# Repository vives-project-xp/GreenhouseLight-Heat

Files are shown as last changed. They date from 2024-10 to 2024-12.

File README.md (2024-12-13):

# GreenhouseLight-Heat

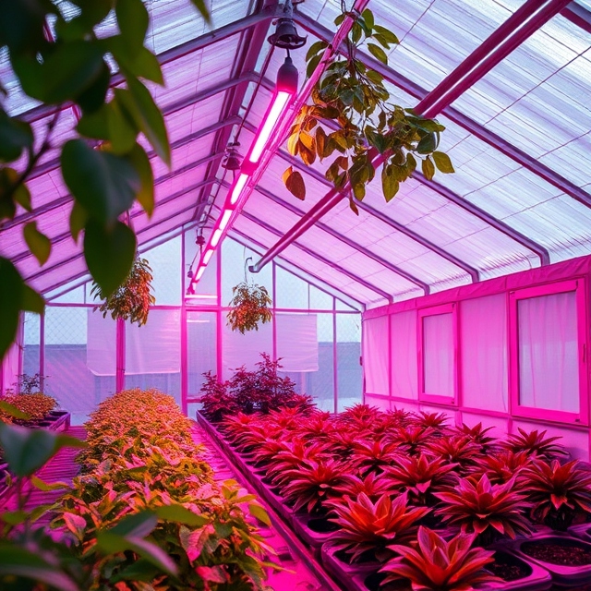
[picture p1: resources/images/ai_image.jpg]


## Introduction

This project automates the control of light and heat within a greenhouse to optimize plant growth year-round. Through a network of sensors and actuators, the system continuously monitors and adjusts environmental conditions to create the ideal environment for plants. We don't do everyting on or own we have a group that measure the temprature and light intensity. And one that send us the data.

[GreenhouseSensoring](./Documentatie/README.md).

[GreenhouseNetwork-Monitoring](https://github.com/vives-project-xp/GreenhouseNetwork-Monitoring).

## Our team

- Thibaut Schroyens (SCRUM Master)
- Sam De Wispelaere
- Joren Vandewalle

## features

- **Light Control:** Automated purple lightning based on the current lightintensity.
- **Temperature Regulation:** Monitors greenhouse temperature, controlling electric heaters to add warmth and a shade cloth to try and cooldown the serre.
- All LEDs, heaters, and actuators run on standard power (230V), making installation straightforward and accessible without specialized wiring.

## Hardware

- **ledstrip:** SK6812 RGBW LED Strip 5m
- **esp32:** ESP32-C3-DevKitC-02
- **voedingen:** Mean Well Rs-50-5 (5V-10A) + Mean Well UHP-200R-36 (36V-5.6A)
- **stappenmotor:** SY42STH47-1206A 
- **level shifter:** Sparkfun Logic converter, bi-directional
- **heater:** VONROC heater marsili compact -2000W
- **Smart plug :** Wiz Smart plug
- **stepper motor driver:** Joy-it SBC-MD-TB6600
- **Shade cloth**
- **Lamp construction**
- **Shade cloth roll-up construction**

### Hardware architecture diagram

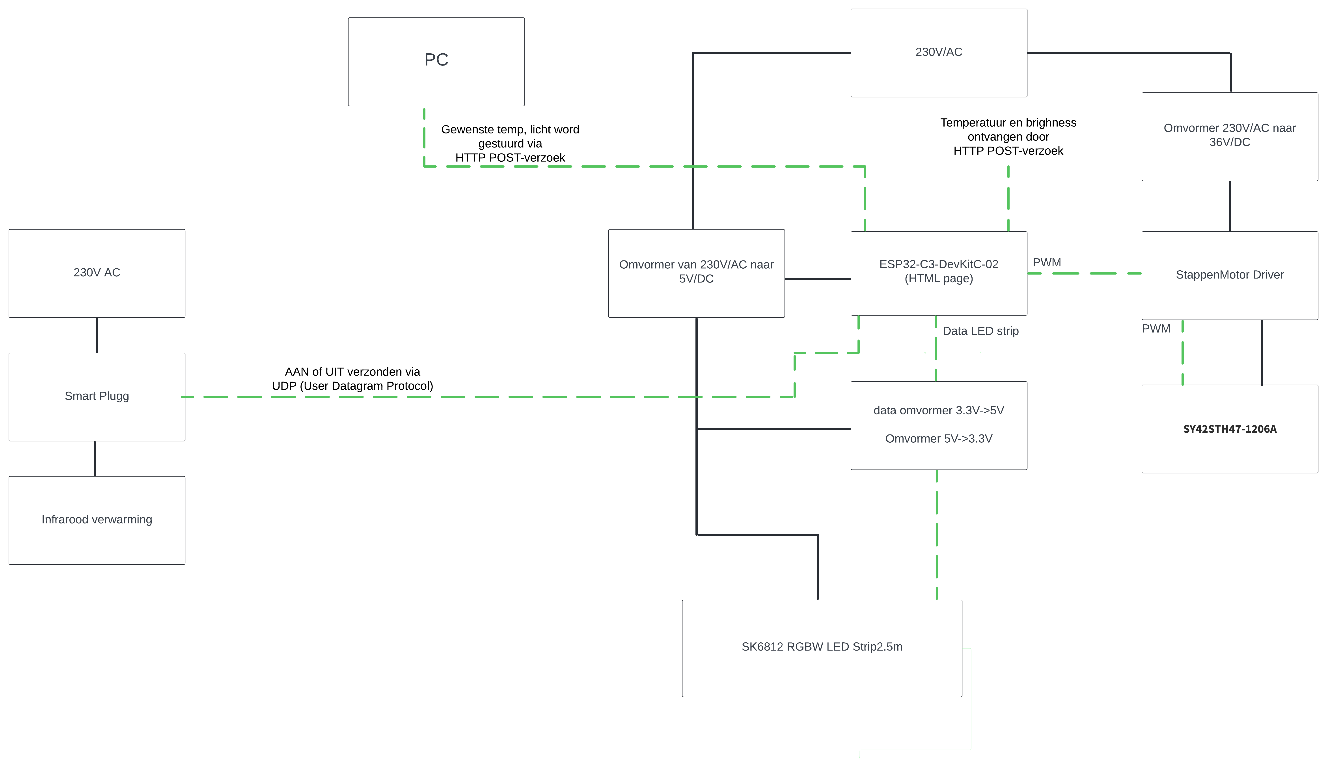
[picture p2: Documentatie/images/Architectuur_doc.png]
Architectuur_Doc


## Software

- We flash all the code on the ESP using  [Arduino IDE](https://www.arduino.cc/en/software). 

We use there settings for our ESP32 in IDE

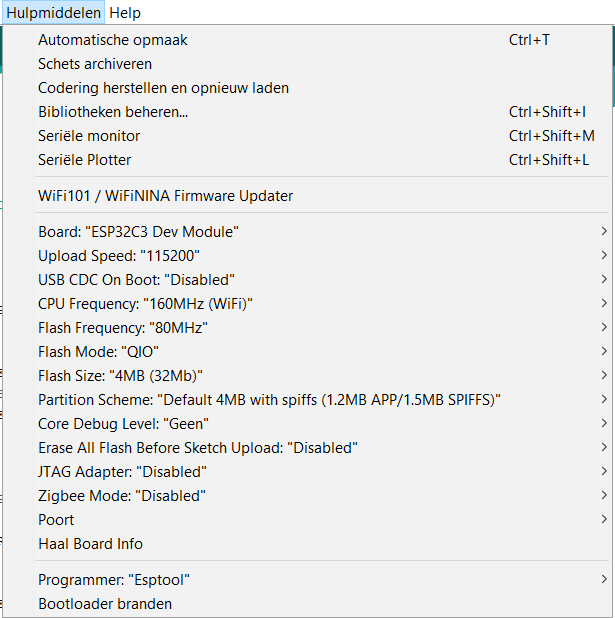
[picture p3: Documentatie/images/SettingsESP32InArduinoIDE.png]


### Used librarys
- **WebServer.h:** Handles HTTP server requests
- **ArduinoJson.h:** Parses incoming JSON data.
- **WiFi.h:** Connects the ESP32 to a Wi-Fi network
- **FastLED.h:** Controls the LED strip.
- **WiFiUdp.h:** Used to communicate with the WiZ smart plug via UDP.

## Bom list

These are all the components we purchased in this project. **Prices may vary depending in the website and date!!**

| Component | Quantity | Price / unit |
| :--- | :---: | ---: |
| [**SK6812 RGBW LED Strip**](https://www.btf-lighting.com/collections/sk6812-rgbw/products/1-sk6812-rgbw-4-in-1-pixels-individual-addressable-led-strip-dc5v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) | 1 | €36,36 |
| [**ESP32-C3-DevKitC-02**](https://www.digikey.be/nl/products/detail/espressif-systems/ESP32-C3-DEVKITC-02/14553009) | 1 | €7,12 |
| [**stappenmotor**](https://www.pololu.com/product/1200l) | 2 | €25,63 |
| [**verwarmingselement**](https://www.brico.be/nl/tuin-terras-buitenleven/terrasverwarming/terrasverwarmers-accessoires/terrasverwarmers/vonroc-heater-marsili-compact-2000w-zwart/10138731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) | 1 | €41,28 |
| [**level shifter**](https://www.kiwi-electronics.com/nl/sparkfun-logic-level-converter-bi-directional-3154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) | 1 | €3,51 |
| [**Omvormer 230-5**](https://www.conrad.be/nl/p/mean-well-rs-50-5-schakelnetvoedingsmodule-5-v-dc-10-a-50-w-1297303.html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) | 1 | €14,04 |
| [**Smart plug**](https://www.hubo.be/nl/p/wiz-smart-plug-stekker/943560/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) | 1 | €13,21 |
| [**Stappenmotordriver**](https://www.conrad.be/nl/p/joy-it-sbc-md-tb6600-stappenmotordriver-2999126.html?refresh=true) | 1 | €19,83 |
| [**voeding driver**](https://www.conrad.be/nl/p/mean-well-uhp-200r-36-schakelnetvoedingsmodule-36-v-dc-5-6-a-201-6-w-2237833.html) | 1 | €54,54 |

## Step by step plan

For a step by step installition guide click [here](./Documentatie/README.md).

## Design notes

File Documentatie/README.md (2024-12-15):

# Installation

## Reviece the data

Before we start we need to be abled to connect the ESP32 to the Wifi and recieve the data from [GreenhouseNetwork-Monitoring](https://github.com/vives-project-xp/GreenhouseNetwork-Monitoring) 

- For this we had to place  [this code snipped](../Code/Sending_date.py) in there code. For more info go to there Github.

- Now to connect the ESP32 to the Wifi and recieve the date we u need to upload [this code snipped](../Code/ResieveData_And_No_WLED/ResieveData_And_No_WLED.ino)  to the esp.

### Postman
- If u dont want to use the other projects or u want to test things without them u can test the ESP32 using [Postman](https://www.postman.com/)

Using these settings: 
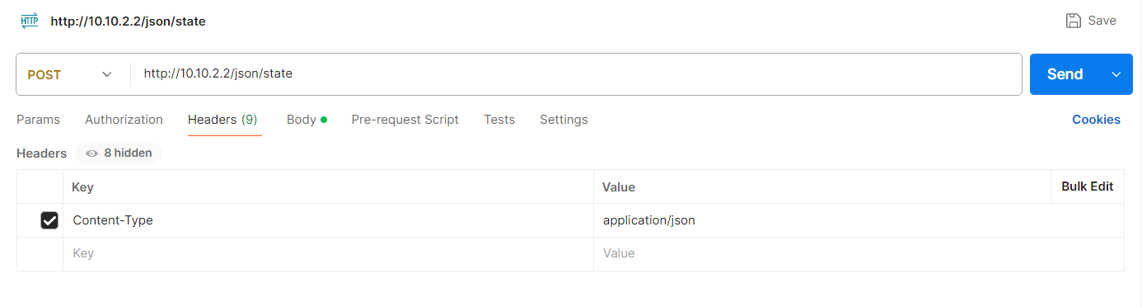
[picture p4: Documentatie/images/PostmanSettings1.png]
Postman1

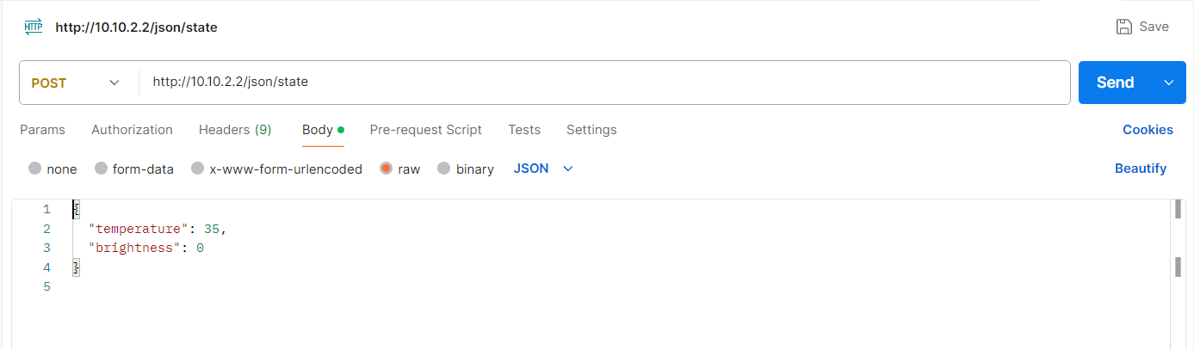
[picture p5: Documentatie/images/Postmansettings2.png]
Postman2


Now u shoud be abled to send the data to ur ESP. 

## Step by step guide

1. **Install the LED strip/Lamp:** this can all be found [here](./Lamp_Install_Guide/README.md)
2. **Install shade Shade cloths:** how to install them can be found here [here](./Shade_cloths_Install_Guide/README.md).
3. **Install heater:** if u want to know how we installed the heater that can be found here [here](./Heater_Install_Guide/README.md).

**Its a good thing to test everyting together in a demo setup before u install things on the actual serre!!!** 

The final code can be found [here](../Code/TotalCode/TotalCode.ino).

### HTML page
Last minute we also put a small HTML page on our ESP , so we can change the wanted temprature in the serre without needing to touch the ESP. If u want to add the HTML page aswell [its this code](../Code/TotalCode/TotalCodeWithHTML/TotalCodeWithHTML.ino) 

### Electrical diagram

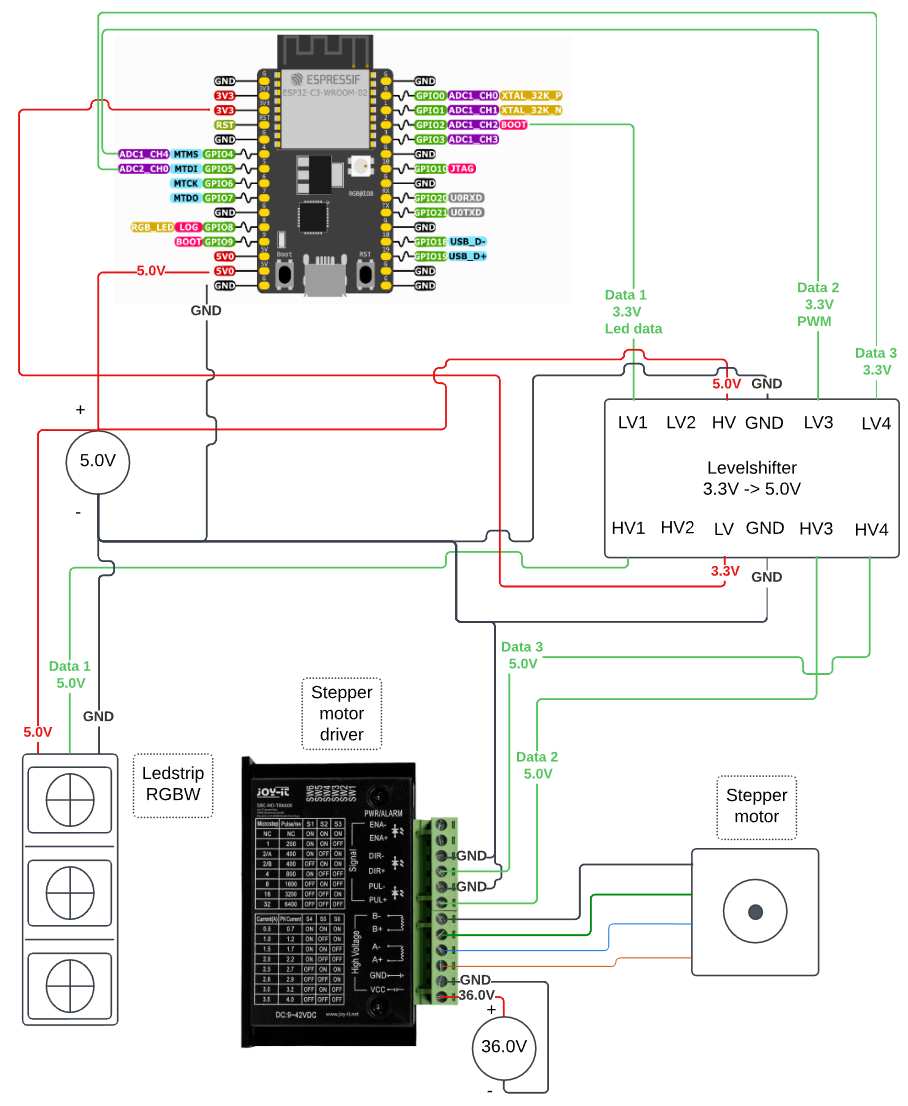
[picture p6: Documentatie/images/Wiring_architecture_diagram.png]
Architectuur_Doc

connections_circuit
connections_circuit

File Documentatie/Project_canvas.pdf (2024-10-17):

Project name GreenhouseLight-Heat | Project owner Vives

Purpose

Whatis the intent ofthis project? Why are we doing this project?

Scope

What does this project contain? What does this project not contain?

| Success Criteria What do we need to achieve in orderfor the project to be successful? How can the Success Criteria be measured?

Milestones

When will we startthe project and when is the final deadline ? What are the key milestones and when willthey occur?
How can the milestones be measured?

Outcome

Whatis the end
result?
- A book
- A website
- An event

Actions

Which activities need to be executed in order to reach a certain milestone?

Team Thibaut Schroyens (Project leader) Who are the team members? What are theirroles in the project? Sam De Wispeleare Joren Vandewalle | Stakeholders Who has an interest in the success of the project? In what way are they involved in the project? Vives | Users Who will benefitfrom the outcome ofthe project? Future students interested in learning about automating processes.
Resources LED lighting, sun-blocking fabric, What resources do we need in the project? - Physical (office, building, server) 12 weeks of work, budget of 175 - Financial (money) euros, positive team. - Human (time, knowledge) | Constraints What are the known limitations ofthe project? - Physical (office, building, server) - Financial (money) -Human (time, knowledge, politics) Money, time, large surfaces. | Risks Which risks may occur during the project? How do we treat these risks? Humidity/wet environment combined with electrical components.
Copyright © Project Canvas | www.projectcanvas.dk

Optimize the growth of plants by adjusting light and heat.

Light and heat regulation.

A fully automated system that optimizes the growth of plants.

Sprint 1: Brainstorming, concept development. Drafting the architecture document, creating a small prototype. Finalize the architecture document, place orders. (3 weeks)
Sprint 2: Working prototype, refined architecture document, final approval. (3 weeks)
Sprint 3: Completed product or proof of concept, thorough documentation, user manual. (3 weeks)
Sprint 4: Product tested, presentation. (2 weeks)
- Research techniques for regulating heat and light.
- Look into how everything can be mounted or installed.
- Explore how to automate the entire system.
- Identify and order the necessary products.
- Document everything as thoroughly as possible.
- Build a prototype to identify where adjustments are needed.

A fully
automated
system that
regulates
temperature
and light in the
greenhouse.

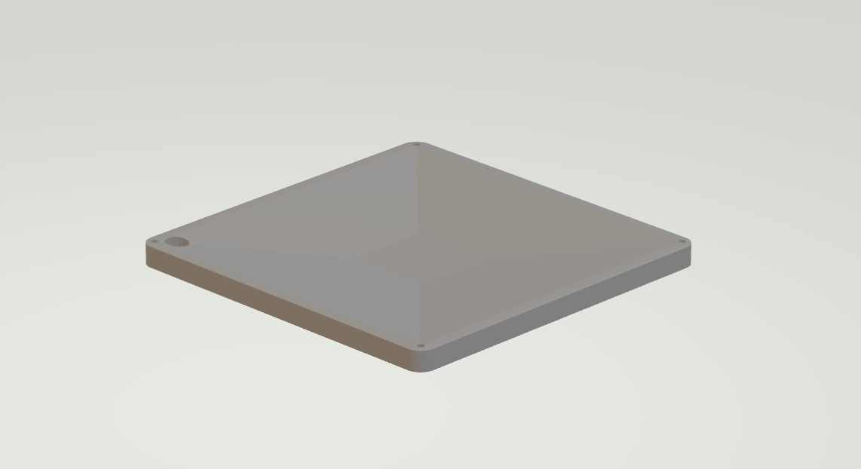
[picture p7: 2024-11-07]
resources/images/LampPlaat.png

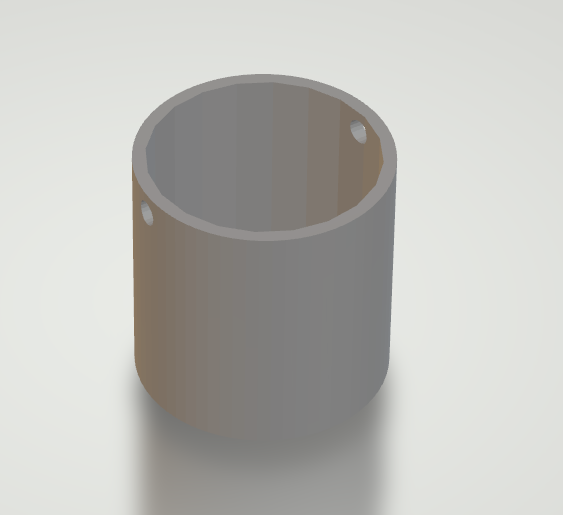
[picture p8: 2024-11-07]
resources/images/WeightForDirt.png

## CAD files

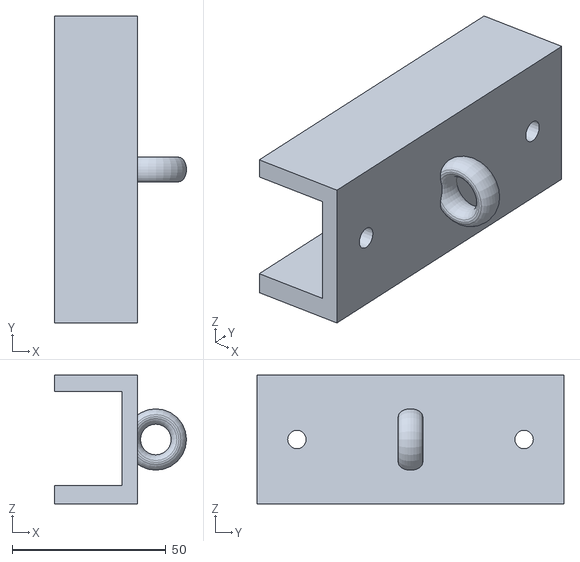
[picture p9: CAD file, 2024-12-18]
resources/3D-Tekeningen/lamp_mount_AND_weight_holder.stl
43.0 x 100.0 x 42.0

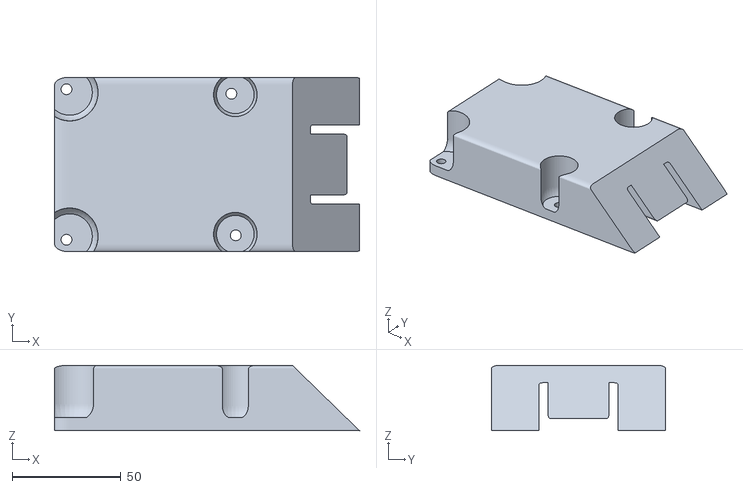
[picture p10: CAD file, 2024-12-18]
resources/3D-Tekeningen/motor_mount_backplate.stl
140.0 x 80.0 x 30.0

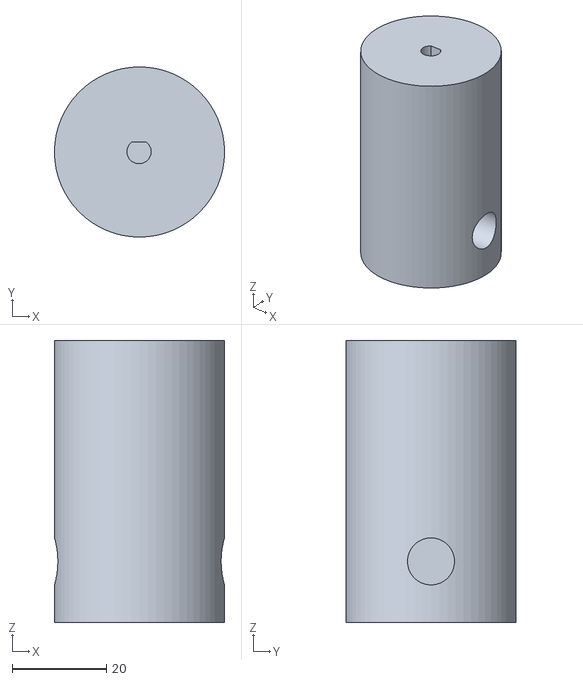
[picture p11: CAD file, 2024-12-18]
resources/3D-Tekeningen/buizen_motor_connect.stl
36.2 x 36.2 x 60.0

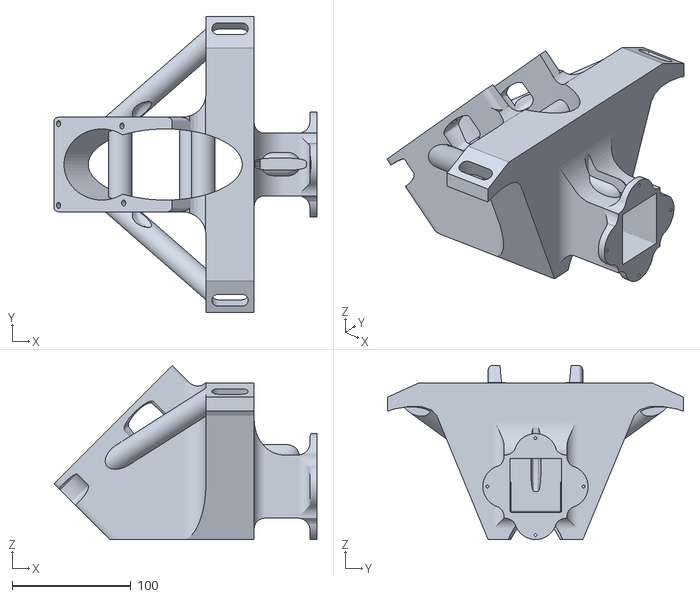
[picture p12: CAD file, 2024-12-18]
resources/3D-Tekeningen/motor_mount.stl
221.9 x 250.0 x 146.9

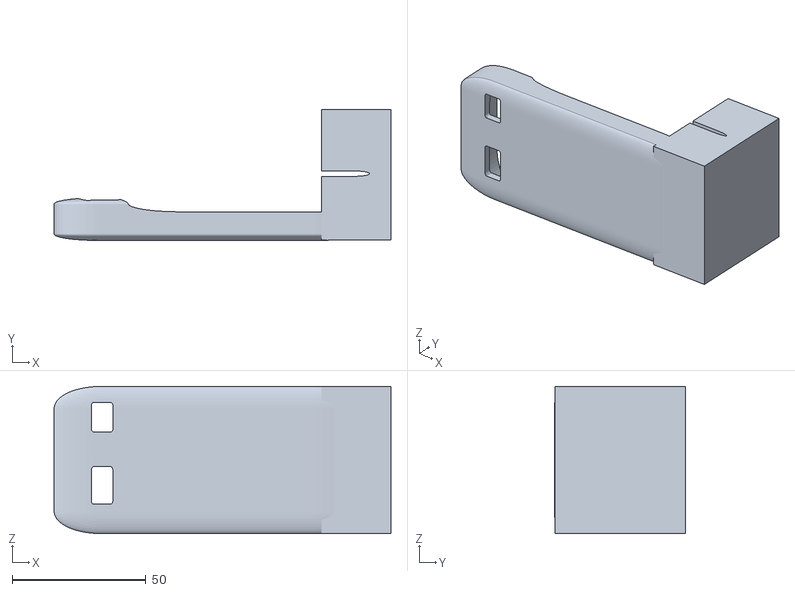
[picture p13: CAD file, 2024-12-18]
resources/3D-Tekeningen/verwarming_mount.stl
126.0 x 49.0 x 55.0

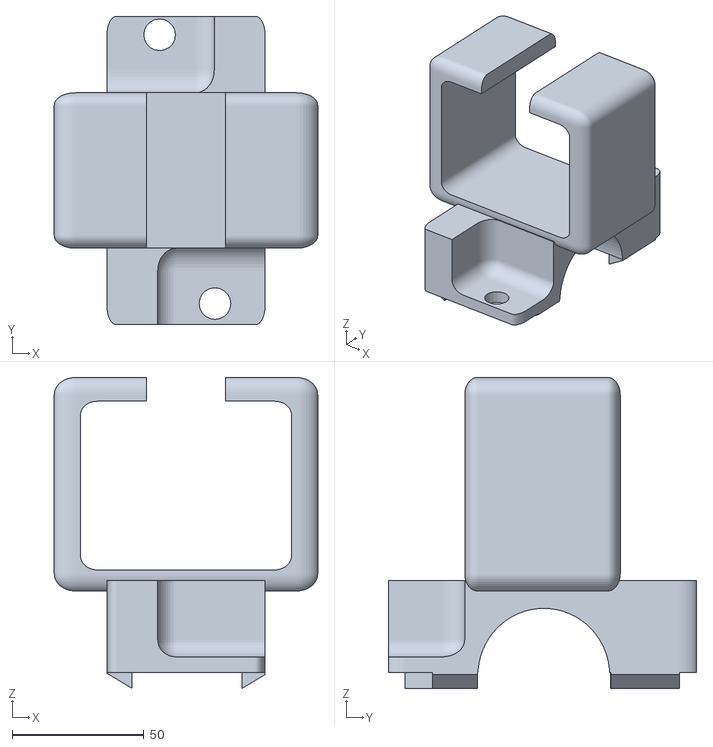
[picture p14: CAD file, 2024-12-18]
resources/3D-Tekeningen/buis_bottom_camera_mount.stl
100.0 x 117.0 x 118.0

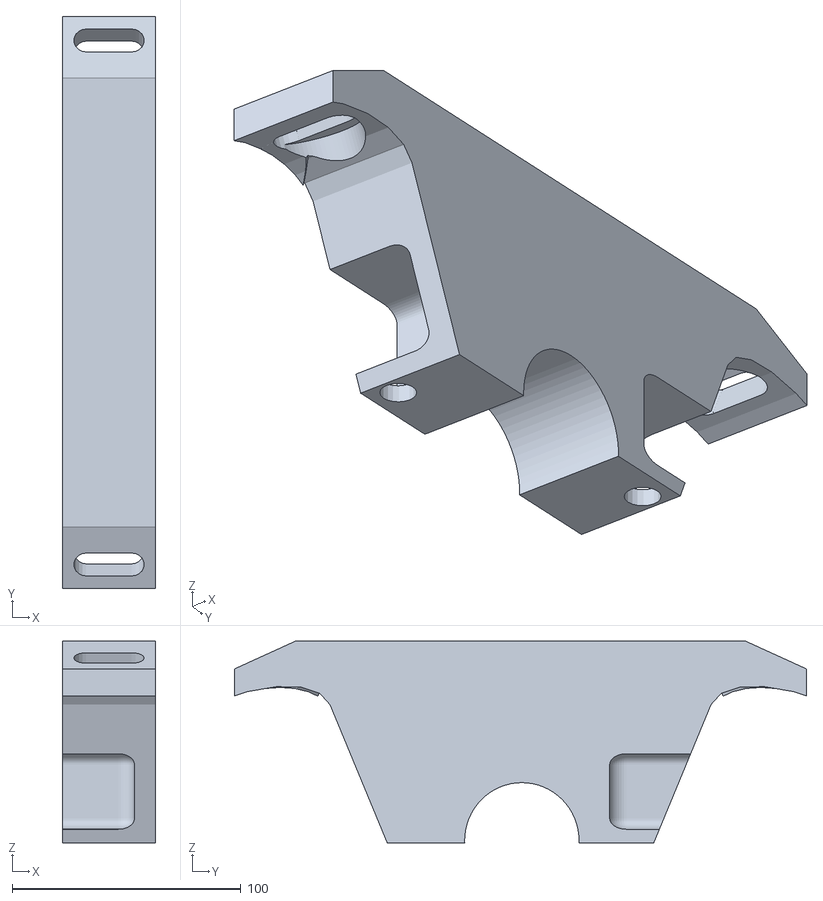
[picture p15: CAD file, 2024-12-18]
resources/3D-Tekeningen/buis_top_camera_mount.stl
40.7 x 250.0 x 88.3

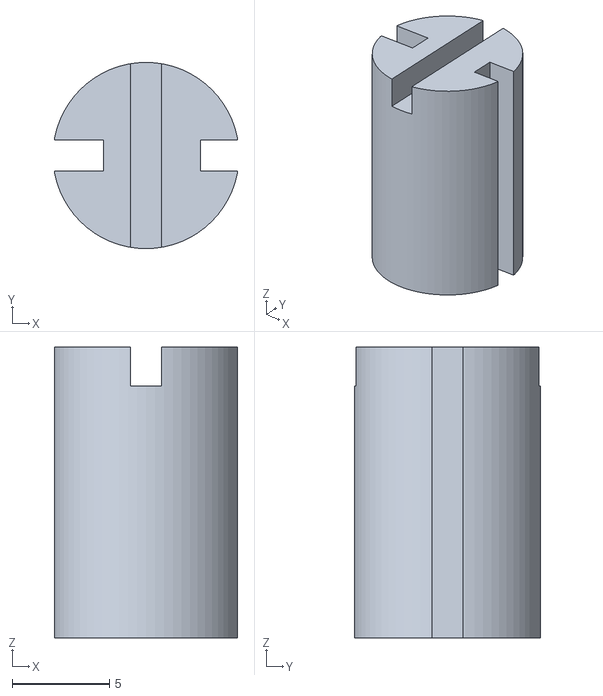
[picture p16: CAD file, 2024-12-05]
resources/3D-Tekeningen/buizen_connector_pins.stl
9.46 x 9.60 x 15.0

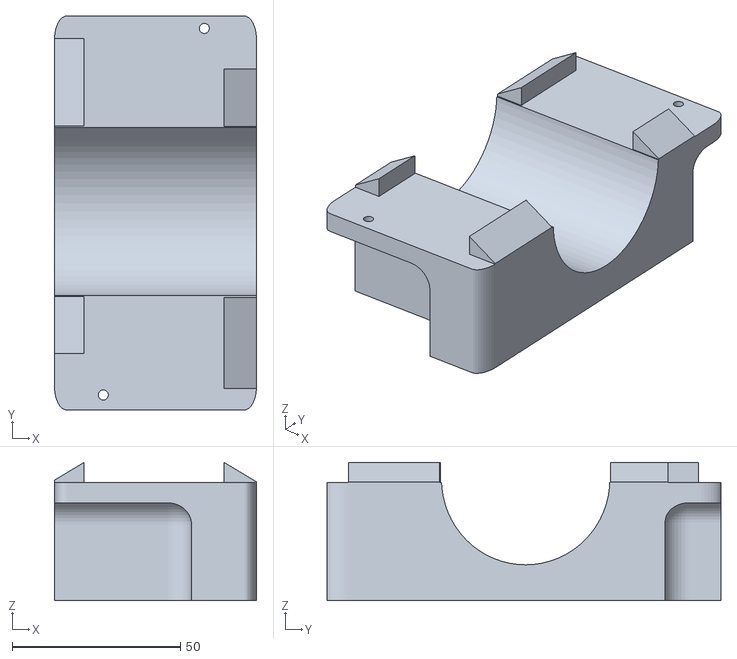
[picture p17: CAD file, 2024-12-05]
resources/3D-Tekeningen/buis_support_bottom.stl
60.0 x 117.0 x 41.0

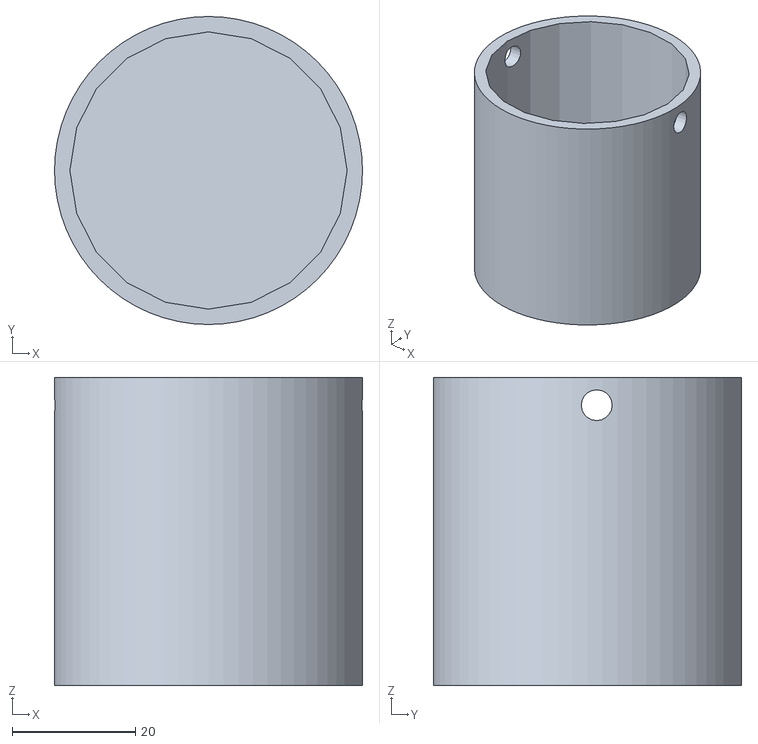
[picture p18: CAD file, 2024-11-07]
resources/3D-Tekeningen/WeightForDirt.stl
50.0 x 50.0 x 50.0

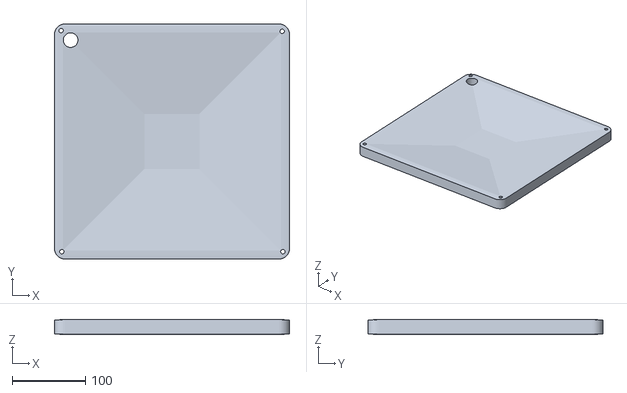
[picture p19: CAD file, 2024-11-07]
resources/3D-Tekeningen/PlaatLamp.stl
320.0 x 320.0 x 20.0

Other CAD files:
resources/3D-Tekeningen/lamp_mount.stl
resources/3D-Tekeningen/buis_support_top.stl
resources/3D-Tekeningen/buizen_connector.stl

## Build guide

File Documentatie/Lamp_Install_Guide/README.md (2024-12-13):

# Install LED strip/Lamp

## Requirements

1. **ledstrip: SK6812 RGBW LED Strip 5m**
2. **SparkFun Logic Level Converter - Bi-Directional**
3. **Soldering material** (Soldering iron, Tin)
4. **ESP32 Microcontroller**
5. Connection cables

## Step 1: Cut and Prepare the LED Strip

Start by cutting the LED strip into 2.5-meter sections. Afterward, cut each 2.5-meter piece into smaller segments, each containing 16 LEDs, resulting in 9 pieces in total.

Next, solder the segments together. Make sure to connect the following:

- **Data (Date)** to **Data Input (Din)**
- **Do (Data Output)** to **Din (Data Input)**
- **GND** to **GND** (Ground)

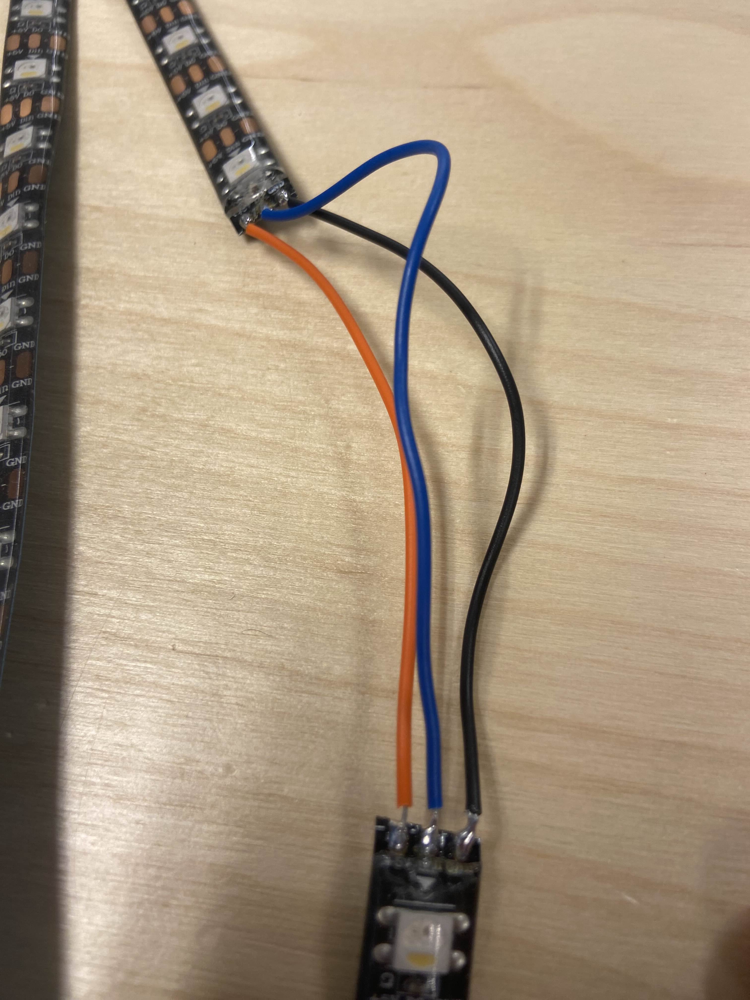
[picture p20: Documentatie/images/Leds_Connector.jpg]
leds_connector


This will ensure that the LED strip is properly configured for your project.

This should be the final result:

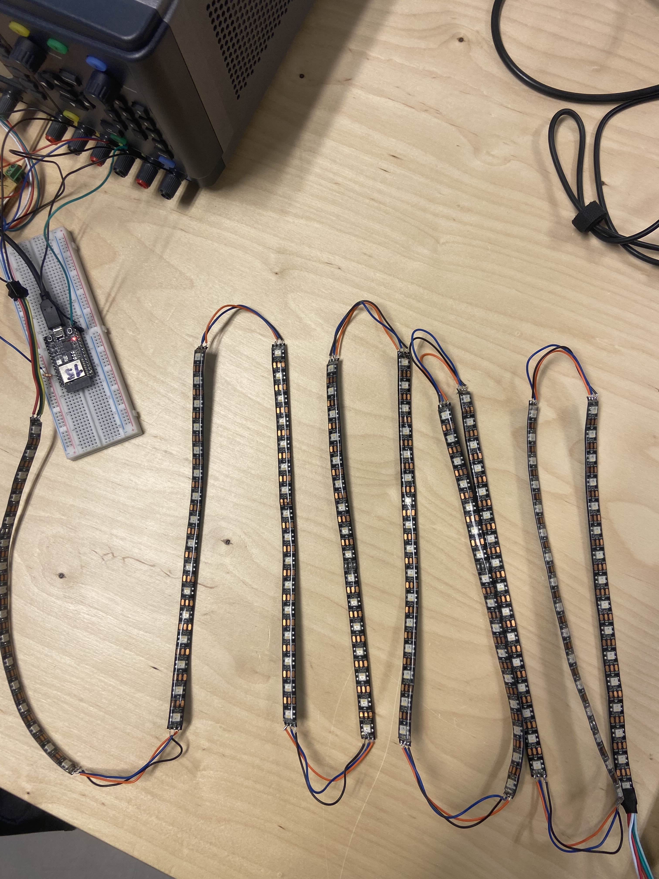
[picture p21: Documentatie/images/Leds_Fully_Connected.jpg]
leds_fully_connected


## Step 2: Connect the LED strip to the ESP32

### Electrical schema

eletrical_schema

electrical_circuit

---

### Guide on Connections

To properly connect the components, we need to use a **3.3V to 5V level shifter** because the ESP32 sends **3.3V data signals**, while the LED strips require **5V data signals**. We made or own custom board for this.

#### Power Supply

- The **5V power source** is used for two purposes:
  1. Supplying power to the **level shifter**.
  2. Feeding power to both the **ESP32** and the **LED strips**.

#### GPIO Connections

- The **LED strip** is connected to **GPIO2** on the ESP32 (via the level shifter).

By ensuring this configuration, the ESP32 can reliably control the LED strips without voltage mismatches.

connections_circuit
connections_circuit

## Step 3: Code

Initially, we considered using **WLED** because it is easy to set up and manage. However, we also needed to implement our custom script on the ESP32 to control the **heater** and **shading**. Since integrating WLED with our custom logic proved challenging, we decided to manage the LEDs through our own script instead. This approach allows us to consolidate all sensor data and control logic.

Then to test the basic LED setup u can [upload this code](../../Code/LEDS_Aanstuuren/LEDS_Appart_Aanstuuren.ino) to ur esp32 this should give u purple light on the LEDS.

## Step 4: Connect the ESP to Net current

## Step 5: Installation on serre

### Led strip on lamp

Now the ledstrip can be put onto the [3d printed lamp](../../resources/3D-Tekeningen/PlaatLamp.stl). You put the ledstrip on the plate of the lamp so that the connector can go true the holes of the plate to connect to the esp on the back side.

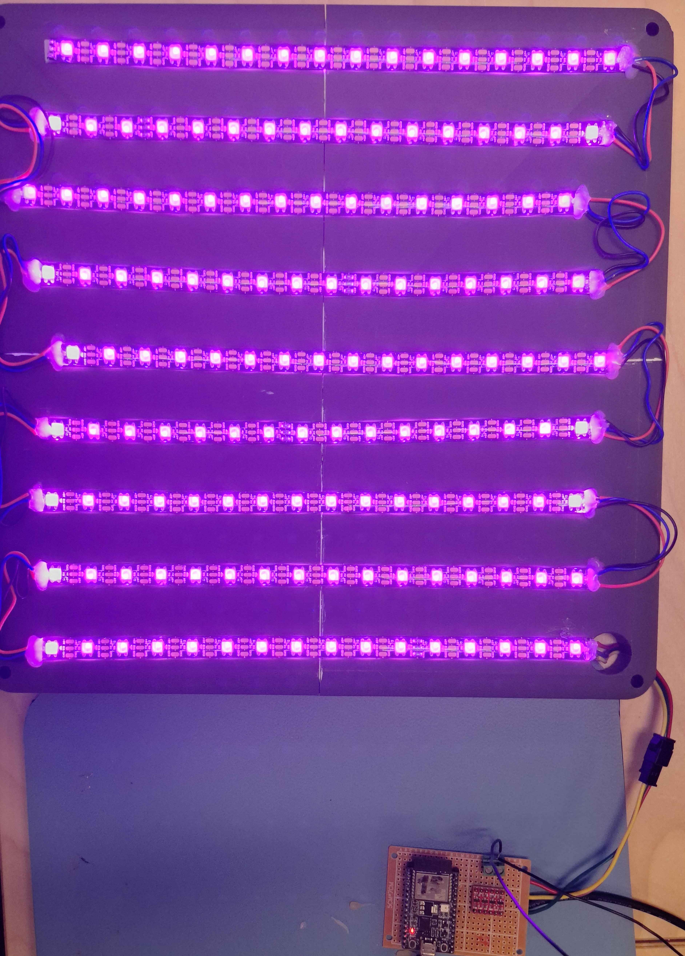
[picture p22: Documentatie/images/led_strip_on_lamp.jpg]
LedStrip_on_Lamp


### Installing it on the serre

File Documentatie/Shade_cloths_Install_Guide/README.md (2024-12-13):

# Install shade Shade cloths

## Requirements

1. **SY42STH47-1206A**
2. **Joy-it SBC-MD-TB6600 Stepper Motor Driver**
3. **Mean Well UHP-200R-36 Power Supply** (36 V, 5.6 A)
4. **ESP32 Microcontroller**
5. Connection cables and optionally: screw terminals or a breadboard.

---

## Step-by-Step Guide

### Step 1 : connecting stepper motor

#### 1. Connecting the Power Supply to the Driver

- Connect the **Mean Well 36 V power supply** to the TB6600 driver's power terminals:
  - **+V**: Connect to the positive output of the power supply.
  - **GND**: Connect to the negative output of the power supply.
- Only turn on the power supply after completing all other connections.

---

#### 2. Connecting the Stepper Motor to the Driver

- Connect the four wires of the SY42STH47-1206A stepmotor to the driver:
  - **A+ and A-**: Connect to the corresponding "A+" and "A-" terminals of the TB6600.

    A+ --> Red 

    A- --> Bleu

  - **B+ and B-**: Connect to the corresponding "B+" and "B-" terminals of the TB6600.

    B+ --> Green

    B- --> Black

- Verify the correct pin order in the motor's datasheet to prevent a short circuit.

---

#### 3. Connecting the ESP32 to the Driver

- Connect the ESP32 to the STEP/DIR inputs of the driver:
  - **DIR+ (Direction)**: Connect to a GPIO pin on the ESP32, for example, GPIO 5.
  - **STEP+ (Pulse)**: Connect to another GPIO pin on the ESP32, for example, GPIO 4.
  - **DIR- and STEP-**: Connect both to the **GND** of the ESP32.
- Ensure the ESP32 and the driver share a common **GND**.

### Images Connections

Architectuur_Doc

## Step 2 : Use the right settings for ur driver

### Setting the DIP Switches on the TB6600

- Configure the DIP switches as follows:
  - **Microstepping**: Choose a desired resolution, such as  microsteps.
  - **Current Limit**: Set the current limit to **1 A**, the nominal current of the SY42STH47-1206A is 1.2A.
- Refer to the TB6600 manual for the correct DIP switch settings.
The following table shows the DIP switch settings for configuring the current limit on the TB6600 driver:

| Current (A) | S4  | S5  | S6  |
|---|---|---|---|
| 0.5 | ON | ON | ON |
| **1.0** | **ON** | **OFF**  | **ON** |
| 1.5 | ON | ON | OFF  |
| 2.0 | ON | OFF  | OFF  |
| 2.5 | OFF  | ON | ON |
| 2.8 | OFF  | OFF  | ON |
| 3.0 | OFF  | ON | OFF  |
| 3.5 | OFF  | OFF  | OFF  |

| Micro Step | Pulse/Rev | S1 | S2 | S3 |
|---|---|---|---|---|
| **1** | **200** | **ON** | **ON** | **OFF**  |
| 2/A | 400 | ON | OFF  | ON |
| 2/B | 400 | OFF  | ON | ON |
| 4 | 800 | ON | OFF  | OFF  |
| 8 | 1600 | OFF  | ON | OFF  |
| 16 | 3200 | OFF  | OFF  | ON |
| 32 | 6400  | OFF  | OFF  | OFF  |

sources:
 https://www.makerguides.com/wp-content/uploads/2019/10/TB6600-Manual.pdf

## Step 3 : Software

### Setting Up Software on the ESP32

- Using the Arduino IDE.

Upload [this code](../../Code/StappenMotorCode/CodeStappenMotorDraaien.ino) to the ESP32 for basic rotation , 1 full rotation right then 1 full rotation left. This way u can varify if it works.

## Step 4 : Installation on serre

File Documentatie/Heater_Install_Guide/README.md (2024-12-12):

# Heater guide

## Requirements

1. **Smart Plug**: we used the [Wiz smart plug](https://www.hubo.be/nl/p/wiz-smart-plug-stekker/943560/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) which is easy to install with a simple guide that comes with the product.
2. **Heater**: we used a [Vonroc heater](https://www.brico.be/nl/tuin-terras-buitenleven/terrasverwarming/terrasverwarmers-accessoires/terrasverwarmers/vonroc-heater-marsili-compact-2000w-zwart/10138731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) because it has a IP55 which is good for outdoor use.
3. **ESP-32**: this is to control the smart plug.

## Step 1: Set up the smart plug

There is an easy installation guide that comes with the product itself. Just plug the smart plug in an outlet and open the app, then click on the plus icon to connect a device, choose for a smart plug. Then you can choose to set it up manually by clicking on the 3 stripes on the rop left corner. Set up the wifi and complete the guide.

## Step 2: Connect the heater to the smart plug

When the smart plug is set up, you can connect the heater to the smart plug. Just plug the heater in and turn it on. If there are anny settings on you heater, you can set them up now to what you think is best. Now you can already control the smart plug and so also the heater from your phone.

## Step 3: Code for ESP-32 to control the smart plug

Via the ESP-32 you can control the smart plug. This is done by sending a HTTP request to the smart plug. [Here](../../Code/Sending_state_to_SP/ESP_To_SmartPlug/ESP_To_SmartPlug.ino) is the code we used to connect and control the smart plug.

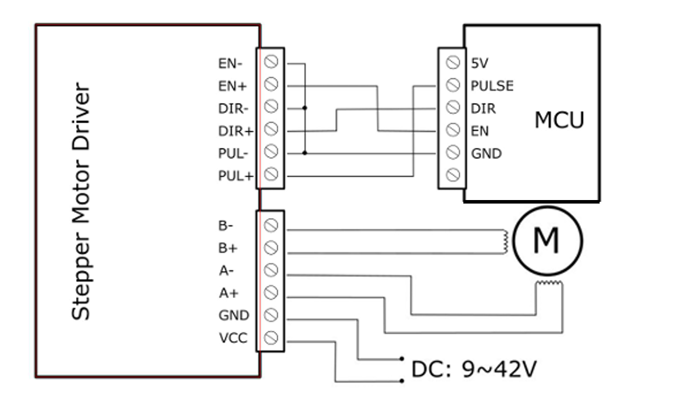
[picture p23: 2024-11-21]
Documentatie/Shade_cloths_Install_Guide/images/Connecting_Stepper_Motor.png

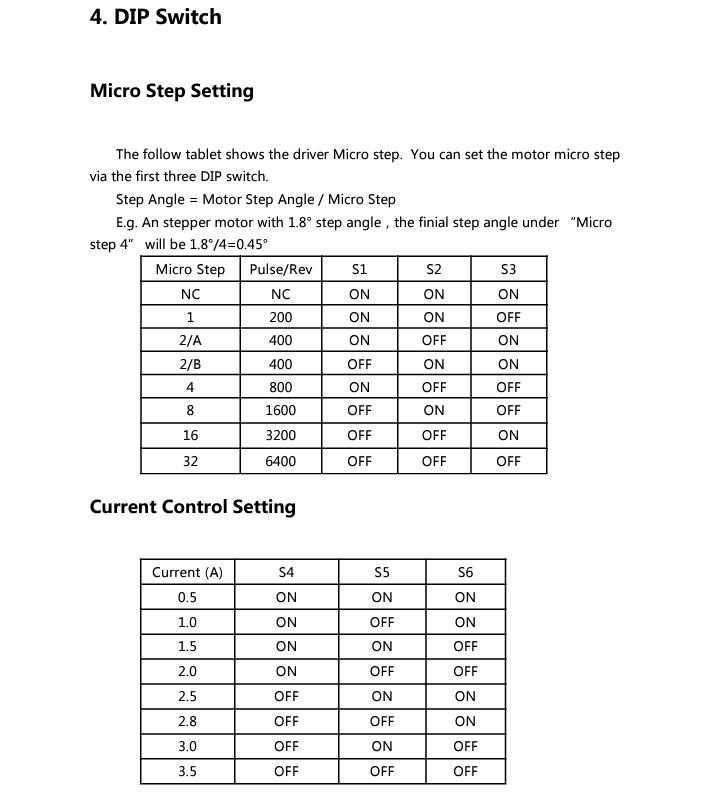
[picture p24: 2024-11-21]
Documentatie/Shade_cloths_Install_Guide/images/Datasheet_DIP_Switches.png

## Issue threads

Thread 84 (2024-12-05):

Hoe RGBW gebruiken

SamDw123, 2024-12-05:
Wij gebruiken een RGBW led strip en geen RGB ledstrip dit zorgt voor problemen.

Closed 2024-12-05.

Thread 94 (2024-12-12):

Uitmeten uitgang esp32 correct

SamDw123, 2024-12-12:
kijken of wat er uit de esp32 komt correct is

Closed 2024-12-12.

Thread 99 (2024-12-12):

Final code Light fix

SamDw123, 2024-12-12:
Aanpassen zodat de LEDs gelijdelijk aan gaan en niet full brightness of uit

Closed 2024-12-12.

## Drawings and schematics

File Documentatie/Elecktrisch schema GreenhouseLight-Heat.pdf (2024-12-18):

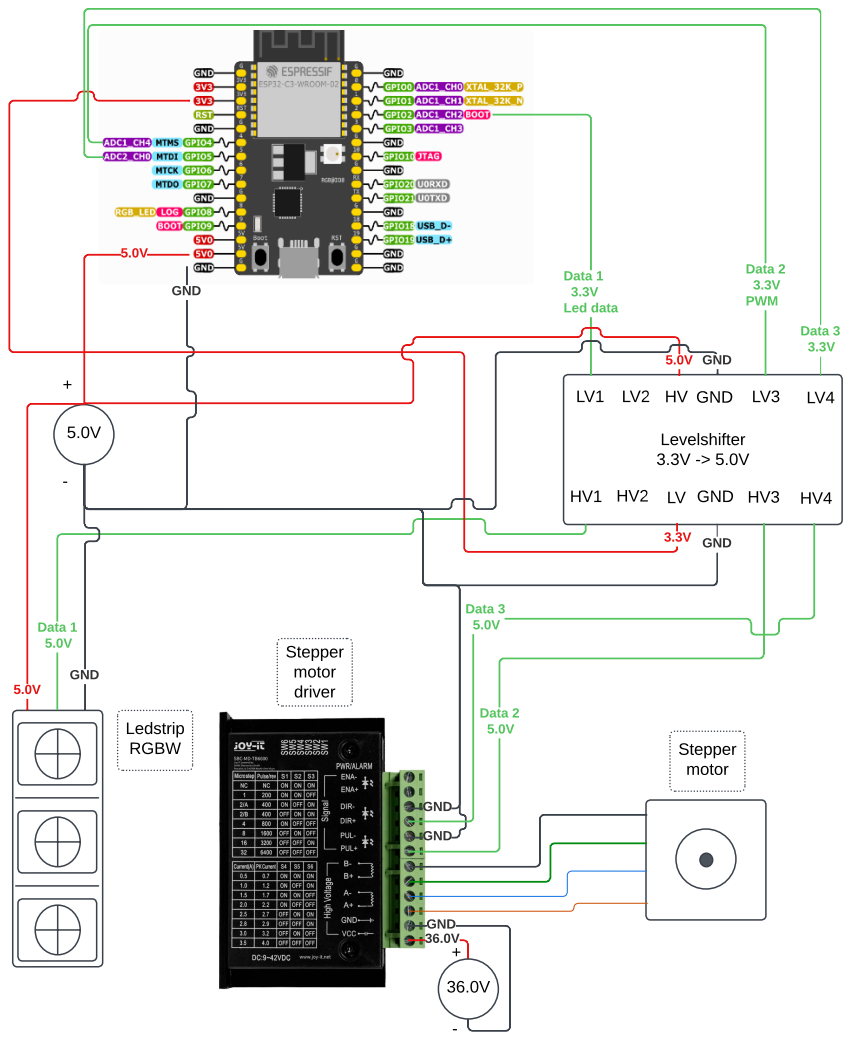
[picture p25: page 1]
Levelshifter 3.3V -> 5.0V; Data 1 5.0V; Ledstrip RGBW; Data 1 3.3V Led data; GND; LV GND; Data 2 3.3V PWM; Data 3 3.3V; GND +; Data 2 5.0V; Data 3 5.0V; Stepper motor; Stepper motor driver

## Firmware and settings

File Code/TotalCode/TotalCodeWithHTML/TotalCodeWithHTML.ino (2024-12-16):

#include <WebServer.h>
#include <ArduinoJson.h>
#include <WiFi.h>       // For ESP32
#include <FastLED.h>
#include <WiFiUdp.h>  // For UDP communication

// Wi-Fi credentials
const char* ssid = "devbit";
const char* password = "Dr@@dloos!";

// Web server
WebServer server(80);
WiFiUDP udp;

// Temperature and brightness values
int OpenShadeAtTemp = 30;  
int CloseShadeAtTemp = 25;
int minValueIdealBrightness = 200;
int maxValueIdealBrightness = 700;
int TurnOnHeater = 20;
int TurnOffHeater = 25;

// kleur instellen
int Rood = 255;
int groen = 0;
int blauw = 255;

#define STEP_PIN 4  // GPIO for STEP+
#define DIR_PIN 5   // GPIO for DIR+

// WiZ smartplug
const char* deviceIP = "10.10.2.77";
const int udpPort = 38899;

long long temperature = -1;
long long brightnessSensor = 500;
int brightnessLEDS = 0;
bool ShadeIsOpen = false;

#define NUM_LEDS 144
#define DATA_PIN 2
CRGB leds[NUM_LEDS];

void setup() {
  Serial.begin(115200);

  // Setup stepper pins
  pinMode(DIR_PIN, OUTPUT);
  pinMode(STEP_PIN, OUTPUT);

  WiFi.disconnect(true);
  delay(1000);
  WiFi.begin(ssid, password);

  Serial.print("Connecting to Wi-Fi");
  while (WiFi.status() != WL_CONNECTED) {
    delay(1000);
    Serial.print(".");
  }
  Serial.println("\nConnected to Wi-Fi!");
  Serial.print("IP Address: ");
  Serial.println(WiFi.localIP());

  // Configure server routes
  server.on("/", handleRoot);
  server.on("/save", HTTP_POST, handleSave);
  server.on("/json/state", HTTP_POST, handleSensorData);

  server.begin();
  Serial.println("HTTP server started");

  FastLED.addLeds<WS2812, DATA_PIN, GRB>(leds, NUM_LEDS).setRgbw(RgbwDefault());

  udp.begin(udpPort);
  Serial.println("UDP Initialized");

  // Set up initial LED state
  for (int i = 0; i < NUM_LEDS; i++) {
    leds[i] = CRGB(Rood, blauw, groen);  // Rood Blauw Groen
  }
  FastLED.show();
}

void handleRoot() {
  char buffer[2048];
snprintf(buffer, sizeof(buffer), R"rawliteral(
<head>
    <title>Instellingen aanpassen</title>
    <meta charset="UTF-8">
</head>
<h1>Pas de waarden aan</h1>
<form action="/save" method="POST">
    <label for="OpenShadeAtTemp">Open Shade At Temp(°C):</label>
    <input type="number" id="OpenShadeAtTemp" name="OpenShadeAtTemp" value="%d"><br>

    <label for="CloseShadeAtTemp">Close Shade At Temp(°C):</label>
    <input type="number" id="CloseShadeAtTemp" name="CloseShadeAtTemp" value="%d"><br>

    <label for="minValueIdealBrightness">Min Value Ideal Brightness:</label>
    <input type="number" id="minValueIdealBrightness" name="minValueIdealBrightness" value="%d"><br>

    <label for="maxValueIdealBrightness">Max Value Ideal Brightness:</label>
    <input type="number" id="maxValueIdealBrightness" name="maxValueIdealBrightness" value="%d"><br>

    <label for="TurnOnHeater">Turn On Heater(°C):</label>
    <input type="number" id="TurnOnHeater" name="TurnOnHeater" value="%d"><br>

    <label for="TurnOffHeater">Turn Off Heater(°C):</label>
    <input type="number" id="TurnOffHeater" name="TurnOffHeater" value="%d"><br>

    <label for="Rood">Rood (0-255):</label>
    <input type="number" id="Rood" name="Rood" value="%d"><br>

    <label for="groen">Groen (0-255):</label>
    <input type="number" id="groen" name="groen" value="%d"><br>

    <label for="blauw">Blauw (0-255):</label>
    <input type="number" id="blauw" name="blauw" value="%d"><br>

    <button type="submit">Opslaan</button>
</form>
)rawliteral",
  OpenShadeAtTemp, CloseShadeAtTemp,
  minValueIdealBrightness, maxValueIdealBrightness,
  TurnOnHeater, TurnOffHeater,
  Rood, groen, blauw);

  server.send(200, "text/html", buffer);
}

void handleSave() {
  if (server.hasArg("OpenShadeAtTemp")) {
    OpenShadeAtTemp = server.arg("OpenShadeAtTemp").toInt();
  }
  if (server.hasArg("CloseShadeAtTemp")) {
    CloseShadeAtTemp = server.arg("CloseShadeAtTemp").toInt();
  }
  if (server.hasArg("minValueIdealBrightness")) {
    minValueIdealBrightness = server.arg("minValueIdealBrightness").toInt();
  }
  if (server.hasArg("maxValueIdealBrightness")) {
    maxValueIdealBrightness = server.arg("maxValueIdealBrightness").toInt();
  }
  if (server.hasArg("TurnOnHeater")) {
    TurnOnHeater = server.arg("TurnOnHeater").toInt();
  }
  if (server.hasArg("TurnOffHeater")) {
    TurnOffHeater = server.arg("TurnOffHeater").toInt();
  }
  if (server.hasArg("Rood")) {
    Rood = server.arg("Rood").toInt();
  }
  if (server.hasArg("groen")) {
    groen = server.arg("groen").toInt();
  }
  if (server.hasArg("blauw")) {
    blauw = server.arg("blauw").toInt();
  }

  // Update LEDs with new color
  for (int i = 0; i < NUM_LEDS; i++) {
    leds[i] = CRGB(Rood, blauw, groen);  // Update LED colors
  }
  FastLED.show();

  Serial.println("Nieuwe waarden ontvangen:");
  Serial.print("OpenShadeAtTemp: "); Serial.println(OpenShadeAtTemp);
  Serial.print("CloseShadeAtTemp: "); Serial.println(CloseShadeAtTemp);
  Serial.print("minValueIdealBrightness: "); Serial.println(minValueIdealBrightness);
  Serial.print("maxValueIdealBrightness: "); Serial.println(maxValueIdealBrightness);
  Serial.print("TurnOnHeater: "); Serial.println(TurnOnHeater);
  Serial.print("TurnOffHeater: "); Serial.println(TurnOffHeater);
  Serial.print("Rood: "); Serial.println(Rood);
  Serial.print("groen: "); Serial.println(groen);
  Serial.print("blauw: "); Serial.println(blauw);

  server.send(200, "text/html", "<h1>Instellingen opgeslagen!</h1><a href='/'>Ga terug</a>");
}


void handleSensorData() {
  StaticJsonDocument<200> doc;

  if (server.hasArg("plain")) {
    DeserializationError error = deserializeJson(doc, server.arg("plain"));
    if (error) {
      server.send(400, "application/json", "{\"error\":\"Invalid JSON\"}");
      return;
    }

    if (doc.containsKey("temperature")) {
      temperature = doc["temperature"];
    }
    if (doc.containsKey("brightness")) {
      brightnessSensor = doc["brightness"];
    }

    Serial.print("Received Temperature: ");
    Serial.println(temperature);
    Serial.print("Received Brightness: ");
    Serial.println(brightnessSensor);

    fixLight();
    fixHeat();

    server.send(200, "application/json", "{\"status\":\"Data received\"}");
  } else {
    server.send(400, "application/json", "{\"error\":\"No body provided\"}");
  }
}

void fixHeat() {
  if (temperature < TurnOnHeater) {
    Serial.println("Temperature below 20°C: Turning smart plug ON");
    sendWiZCommand(true);
  } else if (temperature > TurnOffHeater) {
    Serial.println("Temperature 20°C or above: Turning smart plug OFF");
    sendWiZCommand(false);
  }
  if (temperature > OpenShadeAtTemp && !ShadeIsOpen) {
    OpenShade();
  } else if (temperature < CloseShadeAtTemp && ShadeIsOpen) {
    CloseShade();
  }
}

void fixLight() {
   if (brightnessSensor < minValueIdealBrightness) {
      if (brightnessLEDS >= 235)
      {
        brightnessLEDS = 255;
      } else {
        brightnessLEDS += 10;
      }
      FastLED.setBrightness(brightnessLEDS);
      FastLED.show();
      Serial.print("LEDs more light +10 they are now:");
      Serial.println(brightnessLEDS);
    } 
    else if (brightnessSensor > maxValueIdealBrightness) {
      if (brightnessLEDS <= 20)
      {
        brightnessLEDS = 0;
      } else {
        brightnessLEDS -= 10;
      }
      FastLED.setBrightness(brightnessLEDS);
      FastLED.show();
      Serial.print("LEDs less light (-10) they are now:");
      Serial.println(brightnessLEDS);
    }
}

void sendWiZCommand(bool state) {
  String command = String("{\"method\":\"setState\",\"params\":{\"state\":") + (state ? "true" : "false") + String("}}");

  udp.beginPacket(deviceIP, udpPort);
  udp.print(command);
  udp.endPacket();

  Serial.print("WiZ Command sent: ");
  Serial.println(command);
}


void OpenShade(){
  ShadeIsOpen = true;

  digitalWrite(DIR_PIN, LOW);  // Draairichting vooruit instellen
  Serial.println("Going to OpenShade temp getting high");
  for (int i = 0; i < 2400; i++) { // 200 keer lus doorlopen is 360 graden draaien
    digitalWrite(STEP_PIN, HIGH); // omtrek buizen van ons 12.5 cm doek moet 1.6m uit rollen = ong 12 rotaties = 200*12 = 2400
    delayMicroseconds(1000);  // Snelheid verhogen, kleiner delay
    digitalWrite(STEP_PIN, LOW);
    delayMicroseconds(1000);
  }
}

void CloseShade(){
  ShadeIsOpen = false;

  digitalWrite(DIR_PIN, HIGH);  // Draairichting vooruit instellen
  Serial.println("Going to CloseShade temp getting low");
  for (int i = 0; i < 2400; i++) { // 200 keer lus doorlopen is 360 graden draaien
    digitalWrite(STEP_PIN, HIGH); // omtrek buizen van ons 12.5 cm doek moet 1.6m uit rollen = ong 12 rotaties = 200*12 = 2400
    delayMicroseconds(1000);  // Snelheid verhogen, kleiner delay
    digitalWrite(STEP_PIN, LOW);
    delayMicroseconds(1000);
  }
  digitalWrite(DIR_PIN, LOW);  // Draairichting vooruit instellen
}

void loop() {
  server.handleClient();
  delay(2000);
}

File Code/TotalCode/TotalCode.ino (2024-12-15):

#include <WebServer.h>
#include <ArduinoJson.h>
#include <WiFi.h> // Voor ESP32
#include <FastLED.h>
#include <WiFiUdp.h> // Voor UDP communicatie

// Hieronder vind je de gewenste temp en brightness in de serre 

// De temperatuur waarbij de schaduw automatisch opent om de serre te beschermen tegen oververhitting.
int OpenShadeAtTemp = 30;  

// De temperatuur waarbij de schaduw automatisch sluit als het weer koeler wordt.
int CloseShadeAtTemp = 25; 

// De lichtintensiteit (in sensorwaarden) waarbij de LED-verlichting begin sterker te worden.
int minValueIdealBrightness = 200;  

// De lichtintensiteit (in sensorwaarden) waarbij de LED-verlichting dimt om overbelichting te voorkomen.
int maxValueIdealBrightness = 700;  

// De temperatuur waarbij de kachel automatisch aan gaat om de serre te verwarmen.
int TurnOnHeater = 20;  

// De temperatuur waarbij de kachel automatisch uit gaat als het warm genoeg is.
int TurnOffHeater = 25;


// Stepper instellen
#define STEP_PIN 4  // GPIO voor PUL+
#define DIR_PIN 5    // GPIO voor DIR+

// Wi-Fi-instellingen
const char* ssid = "devbit";       // Wi-Fi SSID
const char* password = "Dr@@dloos!";   // Wi-Fi wachtwoord

WebServer server(80);  // Initialiseer webserver op poort 80
WiFiUDP udp;           // Voor communicatie met de smartplug

// WiZ smartplug-instellingen
const char* deviceIP = "10.10.2.77"; // Vervang met het IP-adres van je WiZ smartplug
const int udpPort = 38899;

// Variabelen om ontvangen gegevens op te slaan
long long temperature = -1; // Begin met een ongeldige waarde
long long brightnessSensor = 500; // Standaard helderheid
int brightnessLEDS = 0;

bool ShadeIsOpen = false;   // als true = schaduw is er over de serre

// LED-instellingen
#define NUM_LEDS 144    // stell het aantal leds in van je ledstri
#define DATA_PIN 2      // stell de pin in van de data naar je leds
CRGB leds[NUM_LEDS];

void setup() {
  Serial.begin(115200);
  
  // stepper als output zetten
  pinMode(DIR_PIN, OUTPUT);
  pinMode(STEP_PIN, OUTPUT);

  // Verbinden met Wi-Fi
  WiFi.disconnect(true); // Zorg dat Wi-Fi losgekoppeld is voor een schone start
  delay(1000);
  WiFi.begin(ssid, password);

  Serial.print("Connecting to Wi-Fi");
  while (WiFi.status() != WL_CONNECTED) {
    delay(1000);
    Serial.print(".");
  }

  Serial.println("\nConnected to Wi-Fi!");
  Serial.print("IP Address: ");
  Serial.println(WiFi.localIP());

  // Configureer de serverroute om JSON-gegevens te ontvangen
  server.on("/json/state", HTTP_POST, handleSensorData);

  // Start de webserver
  server.begin();
  Serial.println("HTTP server started");

  // Initialize LEDs met RGBW-configuratie
  FastLED.addLeds<WS2812, DATA_PIN, GRB>(leds, NUM_LEDS).setRgbw(RgbwDefault());

  // volledige ledstrip op paars zetten
  for (int i = 0; i < NUM_LEDS; i++) {
    leds[i] = CRGB(255, 255, 0); // Paars
  }
  FastLED.show(); // Update de LEDs

  // Initializeer UDP voor de WiZ smartplug
  udp.begin(udpPort);
  Serial.println("UDP Initialized");
}




// Functie om ontvangen JSON-gegevens te verwerken
void handleSensorData() {
  StaticJsonDocument<200> doc;

  if (server.hasArg("plain")) {
    DeserializationError error = deserializeJson(doc, server.arg("plain"));
    if (error) {
      server.send(400, "application/json", "{\"error\":\"Invalid JSON\"}");
      return;
    }

    // Update temperatuur en helderheid alleen bij succesvolle parsing
    if (doc.containsKey("temperature")) {
      temperature = doc["temperature"].as<long long>();
    }
    if (doc.containsKey("brightness")) {
      brightnessSensor = doc["brightness"].as<long long>();
    }

    // Print de ontvangen waarden naar de seriële monitor
    Serial.print("Received Temperature: ");
    Serial.println(temperature);
    Serial.print("Received Brightness: ");
    Serial.println(brightnessSensor);
  
    fixLight();
    fixHeat();

    // Stuur een bevestiging terug naar de client
    server.send(200, "application/json", "{\"status\":\"Data received\"}");
  } else {
    server.send(400, "application/json", "{\"error\":\"No body provided\"}");
  }
}

void fixHeat(){
    // Controleer of de temperatuur onder de 20 graden is
    if (temperature < TurnOnHeater) {
      Serial.println("Temperature below 20°C: Turning smart plug ON");
      sendWiZCommand(true); // Zet de smartplug aan
    } else if(temperature>TurnOffHeater) {
      Serial.println("Temperature 20°C or above: Turning smart plug OFF");
      sendWiZCommand(false); // Zet de smartplug uit
    }
    if (temperature>OpenShadeAtTemp && ShadeIsOpen == false) {
      OpenShade();
    } else if(temperature<CloseShadeAtTemp && ShadeIsOpen == true){
      CloseShade();
    }
}


void fixLight(){
   if (brightnessSensor < minValueIdealBrightness) {
      if (brightnessLEDS >= 235)
      {
        brightnessLEDS = 255;
      } else {
        brightnessLEDS += 10;
      }
      FastLED.setBrightness(brightnessLEDS);
      FastLED.show();
      Serial.print("LEDs more light +10 they are now:");
      Serial.println(brightnessLEDS);
    } 
    else if (brightnessSensor > maxValueIdealBrightness) {
      if (brightnessLEDS <= 20)
      {
        brightnessLEDS = 0;
      } else {
        brightnessLEDS -= 10;
      }
      FastLED.setBrightness(brightnessLEDS);
      FastLED.show();
      Serial.print("LEDs less light (-10) they are now:");
      Serial.println(brightnessLEDS);
    }
}


void OpenShade(){
  ShadeIsOpen = true;

  digitalWrite(DIR_PIN, LOW);  // Draairichting vooruit instellen
  Serial.println("Going to OpenShade temp getting high");
  for (int i = 0; i < 2400; i++) { // 200 keer lus doorlopen is 360 graden draaien
    digitalWrite(STEP_PIN, HIGH); // omtrek buizen van ons 12.5 cm doek moet 1.6m uit rollen = ong 12 rotaties = 200*12 = 2400
    delayMicroseconds(1000);  // Snelheid verhogen, kleiner delay
    digitalWrite(STEP_PIN, LOW);
    delayMicroseconds(1000);
  }
}

void CloseShade(){
  ShadeIsOpen = false;

  digitalWrite(DIR_PIN, HIGH);  // Draairichting vooruit instellen
  Serial.println("Going to CloseShade temp getting low");
  for (int i = 0; i < 2400; i++) { // 200 keer lus doorlopen is 360 graden draaien
    digitalWrite(STEP_PIN, HIGH); // omtrek buizen van ons 12.5 cm doek moet 1.6m uit rollen = ong 12 rotaties = 200*12 = 2400
    delayMicroseconds(1000);  // Snelheid verhogen, kleiner delay
    digitalWrite(STEP_PIN, LOW);
    delayMicroseconds(1000);
  }
}

// Functie om de WiZ smartplug te bedienen
void sendWiZCommand(bool state) {
  // Maak JSON-opdrach

  String command = String("{\"method\":\"setState\",\"params\":{\"state\":") +
                   (state ? "true" : "false") +
                   String("}}");

  // Stuur de opdracht naar de WiZ smartplug
  udp.beginPacket(deviceIP, udpPort);
  udp.print(command);
  udp.endPacket();

  Serial.print("WiZ Command sent: ");
  Serial.println(command);
}
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

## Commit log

2024-11-07 Voorlopige 3D tekening Lamp Plaat
    [LampPlaat.stl]
2024-11-07 3D for Weight housing
    [WeightForDirt.stl]
2024-11-14 current BOM added
2024-11-14 BOM link fix
2024-11-19 fixed a mistake in readme, added sensor data in test.js
2024-11-21 images leds in docs
2024-11-28 added circuit pictures
2024-12-05 3d prints
    [buis_support_bottom.stl, buis_support_top.stl, buizen_connector.stl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]
2024-12-05 Update installation guides for lamp and heater; adjust step numbering and add LED strip instructions
2024-12-07 Update heater installation guide with detailed setup steps for smart plug and ESP-32 control
2024-12-08 Update README.md with link to heater installation guide
2024-12-12 complete code added stepper
2024-12-12 Updated electrical schematic for GreenhouseLight-Heat project
2024-12-12 errors fixed in code
    [TotalCode.ino]
2024-12-14 added full test code with motor code
2024-12-15 Powerpoint Update
2024-12-18 fixed mistake in wiring architecture
